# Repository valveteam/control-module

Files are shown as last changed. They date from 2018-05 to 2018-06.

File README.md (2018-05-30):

# control-module
Control module for the valve

This repository contains;
* The Arduino code for flow control module
* A test file & I2C Scan program for debugging
* CAD File for the control module using an Arduino Micro as the Microcontroller
* CAD File for the control module using an Arduino Nano as the Microcontroller (Outdated)
 
## Notes
* The final design was implemented with the Micro so the CAD files are slightly outdated (the NMOS buffer circuits and additional trimmer not included)

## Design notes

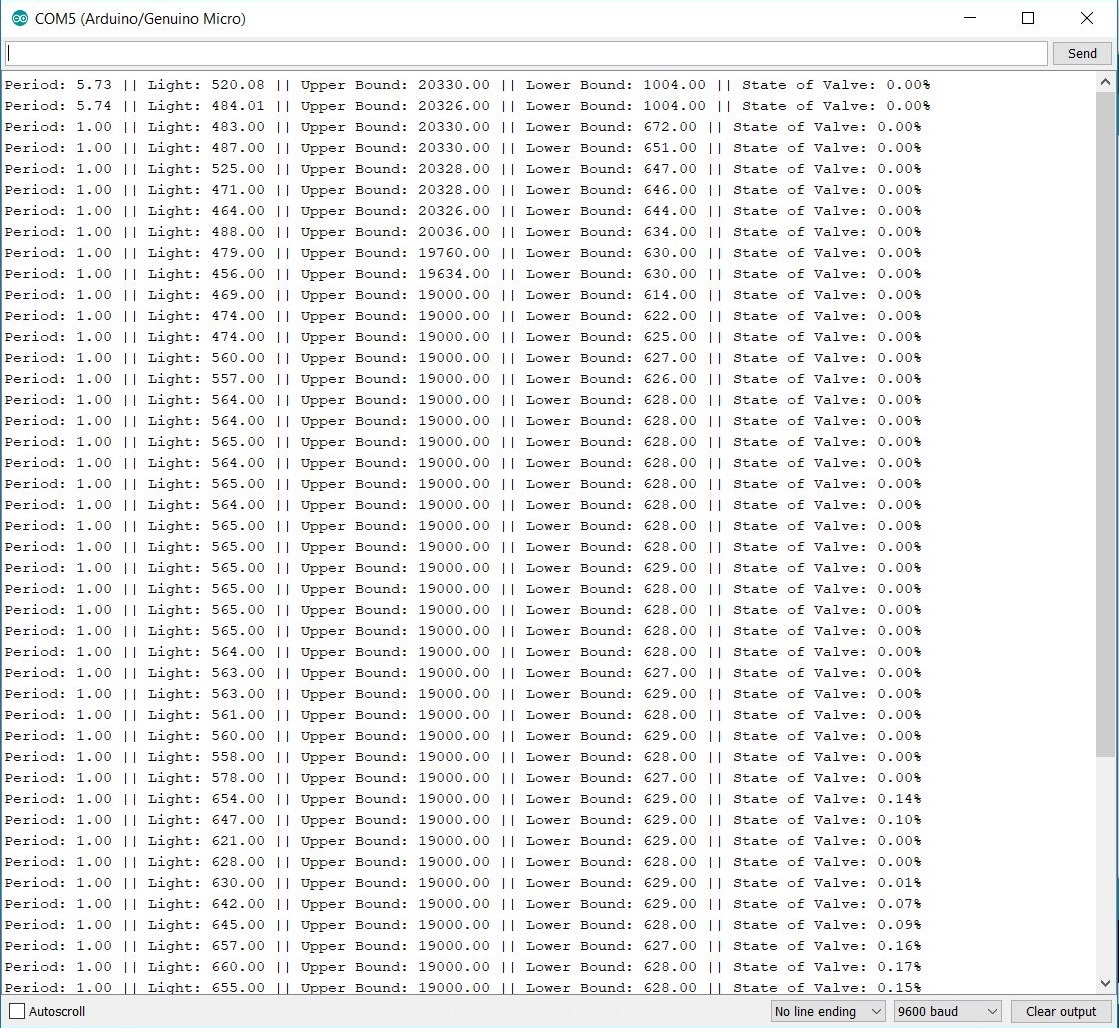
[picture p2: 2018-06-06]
Code/Control/control_bh1750/serial_output.JPG

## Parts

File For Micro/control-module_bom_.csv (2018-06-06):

Component | Description | Part | References | Value | Footprint | Quantity Per PCB | Datasheet
1 | Unpolarized capacitor | C | C1 C2 C3 C4 | 10uF | C_0805_HandSoldering | 4
2 |  | LED-RESCUE-control-module | D1 D2 D3 D4 | LED | LED_0805_HandSoldering | 4
3 |  | I2C-PCA9517 | I2Crepeater1 I2Crepeater2 | I2C-PCA9517 | TSSOP-8_3x3mm_Pitch0.65mm | 2
4 | Generic connector, single row, 01x06 | Conn_01x06 | J1 | For Expansion | Molex_KK-6410-06_06x2.54mm_Straight | 1
5 | Generic connector, single row, 01x06 | Conn_01x06 | J6 | For Flow Module a | Molex_KK-6410-06_06x2.54mm_Straight | 1
6 | Generic connector, single row, 01x06 | Conn_01x06 | J5 | For Flow Module b | Molex_KK-6410-06_06x2.54mm_Straight | 1
7 | Generic connector, single row, 01x06 | Conn_01x06 | J2 | For Light Sensor | Molex_KK-6410-06_06x2.54mm_Straight | 1
8 | Generic connector, single row, 01x02 | Conn_01x02 | J3 | From Solar Panel | TE_TERM | 1
9 | Generic connector, single row, 01x02 | Conn_01x02 | J4 | To Flow Module (F) | TE_TERM | 1
10 | Jumper, normally open | Jumper_NO_Small | JP1 JP2 JP3 | Jumper_NO_Small | SMD-solder-bridge | 3
11 |  | INDUCTOR | L1 L2 | 6.8uH | WURTH_INDUCTOR | 2
12 | Transistor N-MOSFET (general) | Q_NMOS_DGS | Q1 Q2 Q3 Q4 | NMOS | SOT-23_Handsoldering | 4
13 | Resistor | R | R1 R2 | 4.7k | R_0805_HandSoldering | 2
14 | Resistor | R | R4 R5 R6 | 470 | R_0805_HandSoldering | 3
15 | Resistor | R | R3 | 680 | R_0805_HandSoldering | 1
16 | Trim-Potentiometer | POT_TRIM | RV2 | Trimmer Lower | Potentiometer_Trimmer_Vishay_T73XX_Vertical | 1
17 | Trim-Potentiometer | POT_TRIM | RV1 RV3 | Trimmer Upper | Potentiometer_Trimmer_Vishay_T73XX_Vertical | 2
18 | Arduino Micro shield | ARDUINO_MICRO_SHIELD | U3 | ARDUINO_MICRO_SHIELD | ARDUINO_MICRO_SHIELD | 1
19 | Linear Regulator +5V | TR_SERIES | U1 U2 | TR_SERIES | TR_Series | 2 | regulator\lm78xx.pdf
Component Groups: | 19
Component Count: | 37
Fitted Components: | 37
Number of PCBs: | 1
Total components: | 37
Schematic Version:
Schematic Date:
BoM Date: | 04/06/2018 09:44:44
Schematic Source: | C:/Users/tooyi/Dropbox/tfpb/control-module/For Micro/control-module.sch
KiCad Version: | Eeschema 4.0.7

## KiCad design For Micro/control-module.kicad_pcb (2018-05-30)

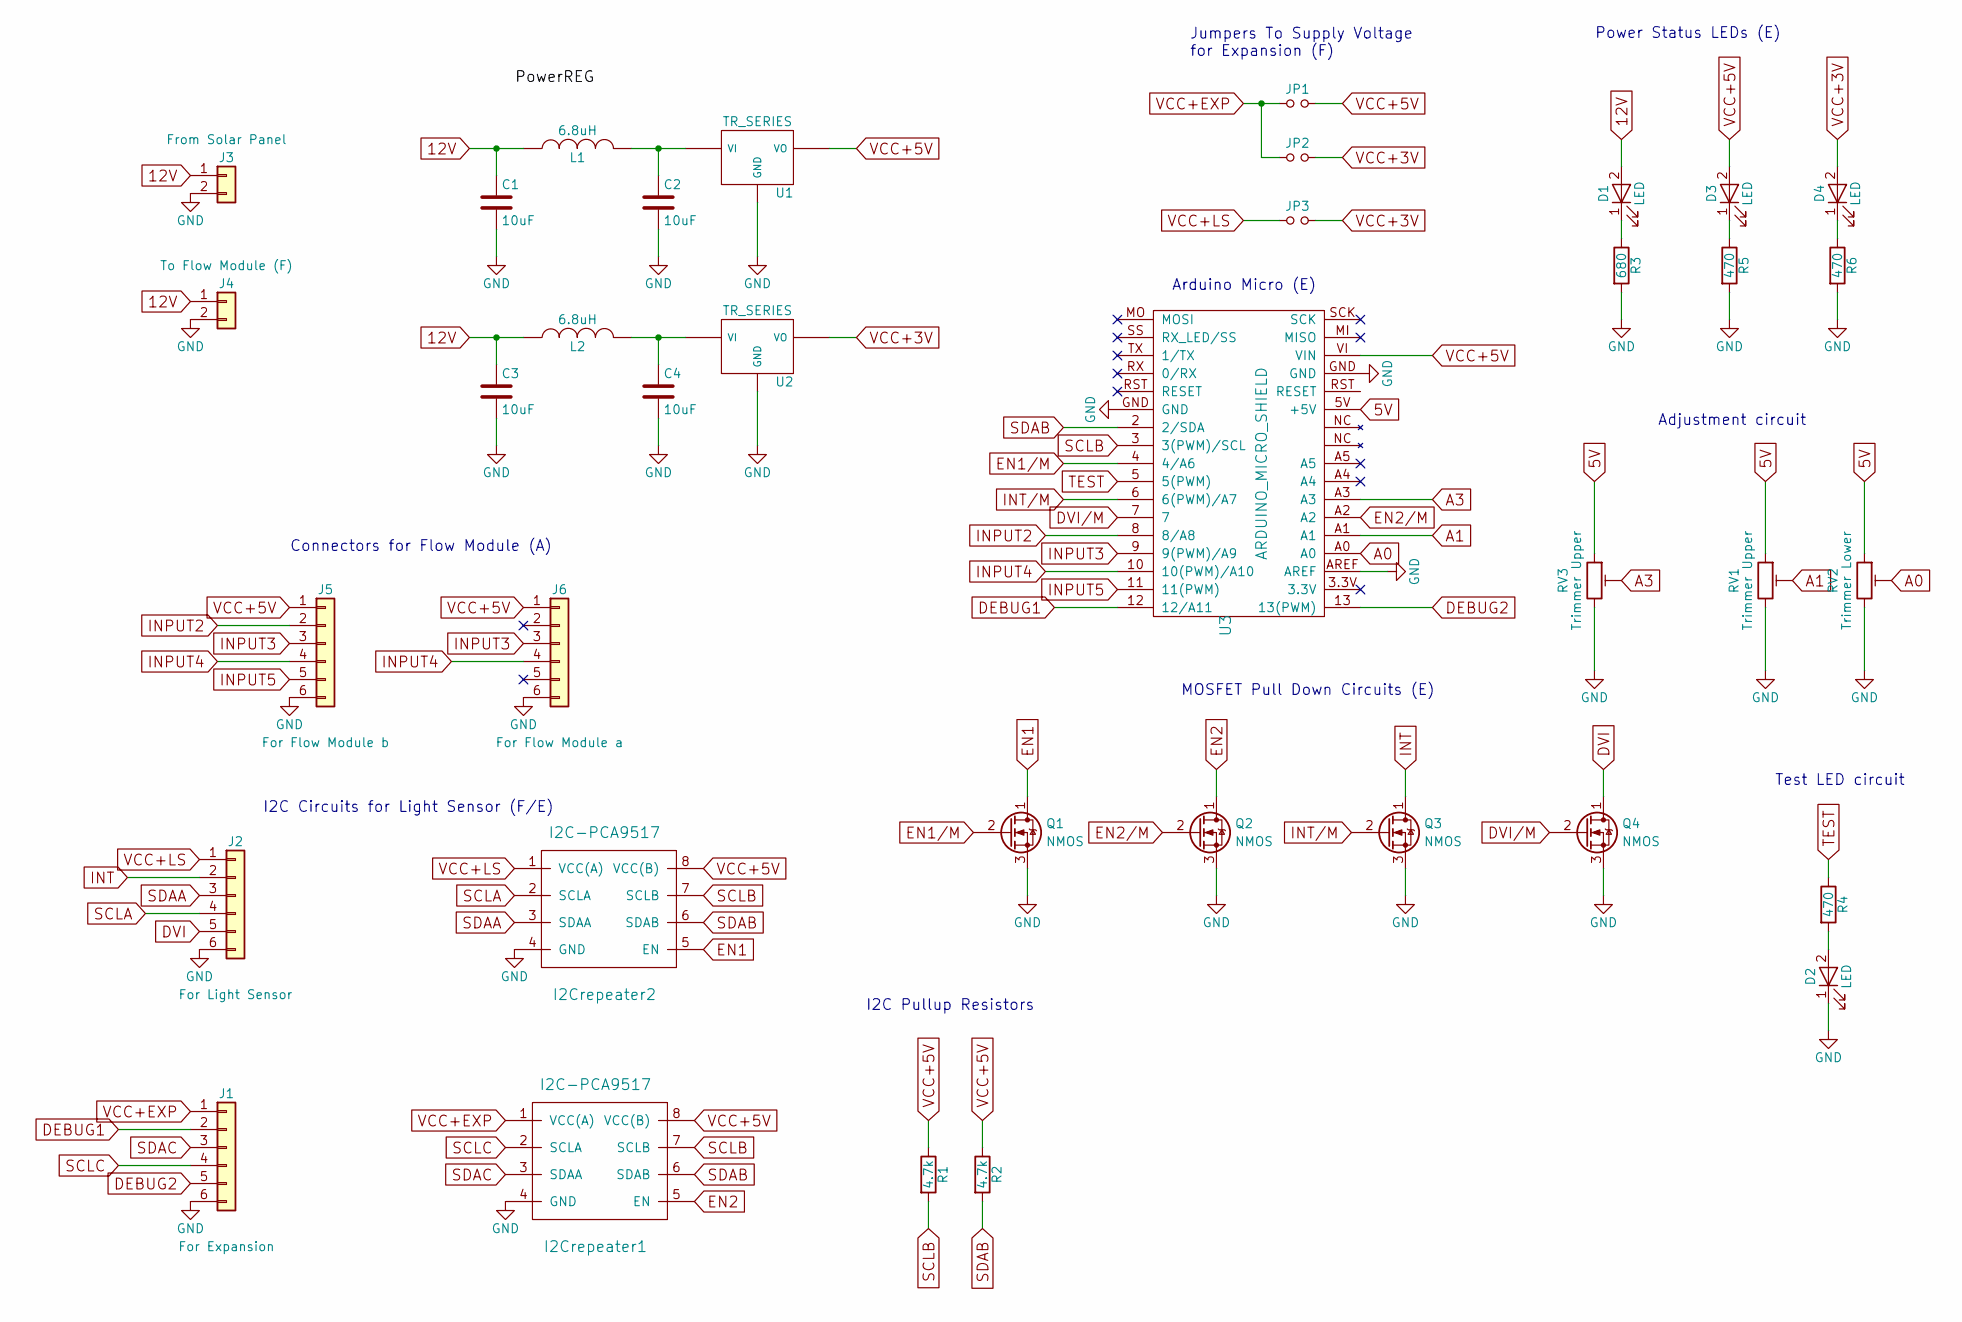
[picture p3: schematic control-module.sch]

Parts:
C1, C2, C3, C4: 10uF; C_0805_HandSoldering
D1, D2, D3, D4: LED; LED_0805_HandSoldering
I2Crepeater1, I2Crepeater2: I2C-PCA9517; TSSOP-8_3x3mm_Pitch0.65mm
J1: For Expansion; Molex_KK-6410-06_06x2.54mm_Straight
J2: For Light Sensor; Molex_KK-6410-06_06x2.54mm_Straight
J3: From Solar Panel; TE_TERM
J4: To Flow Module (F); TE_TERM
J5: For Flow Module b; Molex_KK-6410-06_06x2.54mm_Straight
J6: For Flow Module a; Molex_KK-6410-06_06x2.54mm_Straight
JP1, JP2, JP3: Jumper_NO_Small; SMD-solder-bridge
L1, L2: 6.8uH; WURTH_INDUCTOR
Q1, Q2, Q3, Q4: NMOS; SOT-23_Handsoldering
R1, R2: 4.7k; R_0805_HandSoldering
R3: 680; R_0805_HandSoldering
R4, R5, R6: 470; R_0805_HandSoldering
RV1, RV3: Trimmer Upper; Potentiometer_Trimmer_Vishay_T73XX_Vertical
RV2: Trimmer Lower; Potentiometer_Trimmer_Vishay_T73XX_Vertical
U1, U2: TR_SERIES; TR_Series
U3: ARDUINO_MICRO_SHIELD

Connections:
5V: RV1.1, RV2.1, RV3.1, U3.5V (+5V)
12V: C1.1, C3.1, D1.2 (A), J3.1, J4.1, L1.1, L2.1
A0: RV2.2, U3.A0
A1: RV1.2, U3.A1
A3: RV3.2, U3.A3
DEBUG1: J1.2, U3.12 (12/A11)
DEBUG2: J1.5, U3.13 (13(PWM))
DVI: J2.5, Q4.1 (D)
DVI/M: Q4.2 (G), U3.7
EN1: I2Crepeater2.5 (EN), Q1.1 (D)
EN1/M: Q1.2 (G), U3.4 (4/A6)
EN2: I2Crepeater1.5 (EN), Q2.1 (D)
EN2/M: Q2.2 (G), U3.A2
GND: C1.2, C2.2, C3.2, C4.2, D2.1 (K), I2Crepeater1.4 (GND), I2Crepeater2.4 (GND), J1.6, J2.6, J3.2, J4.2, J5.6, J6.6, Q1.3 (S), Q2.3 (S), Q3.3 (S), Q4.3 (S), R3.2, R5.2, R6.2, RV1.3, RV2.3, RV3.3, U1.GND, U2.GND, U3.AREF, U3.GND
INPUT2: J5.2, U3.8 (8/A8)
INPUT3: J5.3, J6.3, U3.9 (9(PWM)/A9)
INPUT4: J5.4, J6.4, U3.10 (10(PWM)/A10)
INPUT5: J5.5, U3.11 (11(PWM))
INT: J2.2, Q3.1 (D)
INT/M: Q3.2 (G), U3.6 (6(PWM)/A7)
unnamed: C2.1, L1.2, U1.VI
unnamed: C4.1, L2.2, U2.VI
unnamed: D1.1 (K), R3.1
unnamed: D2.2 (A), R4.2
unnamed: D3.1 (K), R5.1
unnamed: D4.1 (K), R6.1
SCLA: I2Crepeater2.2 (SCLA), J2.4
SCLB: I2Crepeater1.7 (SCLB), I2Crepeater2.7 (SCLB), R1.2, U3.3 (3(PWM)/SCL)
SCLC: I2Crepeater1.2 (SCLA), J1.4
SDAA: I2Crepeater2.3 (SDAA), J2.3
SDAB: I2Crepeater1.6 (SDAB), I2Crepeater2.6 (SDAB), R2.2, U3.2 (2/SDA)
SDAC: I2Crepeater1.3 (SDAA), J1.3
TEST: R4.1, U3.5 (5(PWM))
VCC+3V: D4.2 (A), JP2.2, JP3.2, U2.VO
VCC+5V: D3.2 (A), I2Crepeater1.8 (VCC(B)), I2Crepeater2.8 (VCC(B)), J5.1, J6.1, JP1.2, R1.1, R2.1, U1.VO, U3.VI (VIN)
VCC+EXP: I2Crepeater1.1 (VCC(A)), J1.1, JP1.1, JP2.1
VCC+LS: I2Crepeater2.1 (VCC(A)), J2.1, JP3.1

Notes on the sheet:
Adjustment circuit
Test LED circuit
I2C Circuits for Light Sensor (F/E)
Connectors for Flow Module (A)
Power Status LEDs (E)
MOSFET Pull Down Circuits (E)
I2C Pullup Resistors
Arduino Micro (E)
Jumpers To Supply Voltage for Expansion (F)

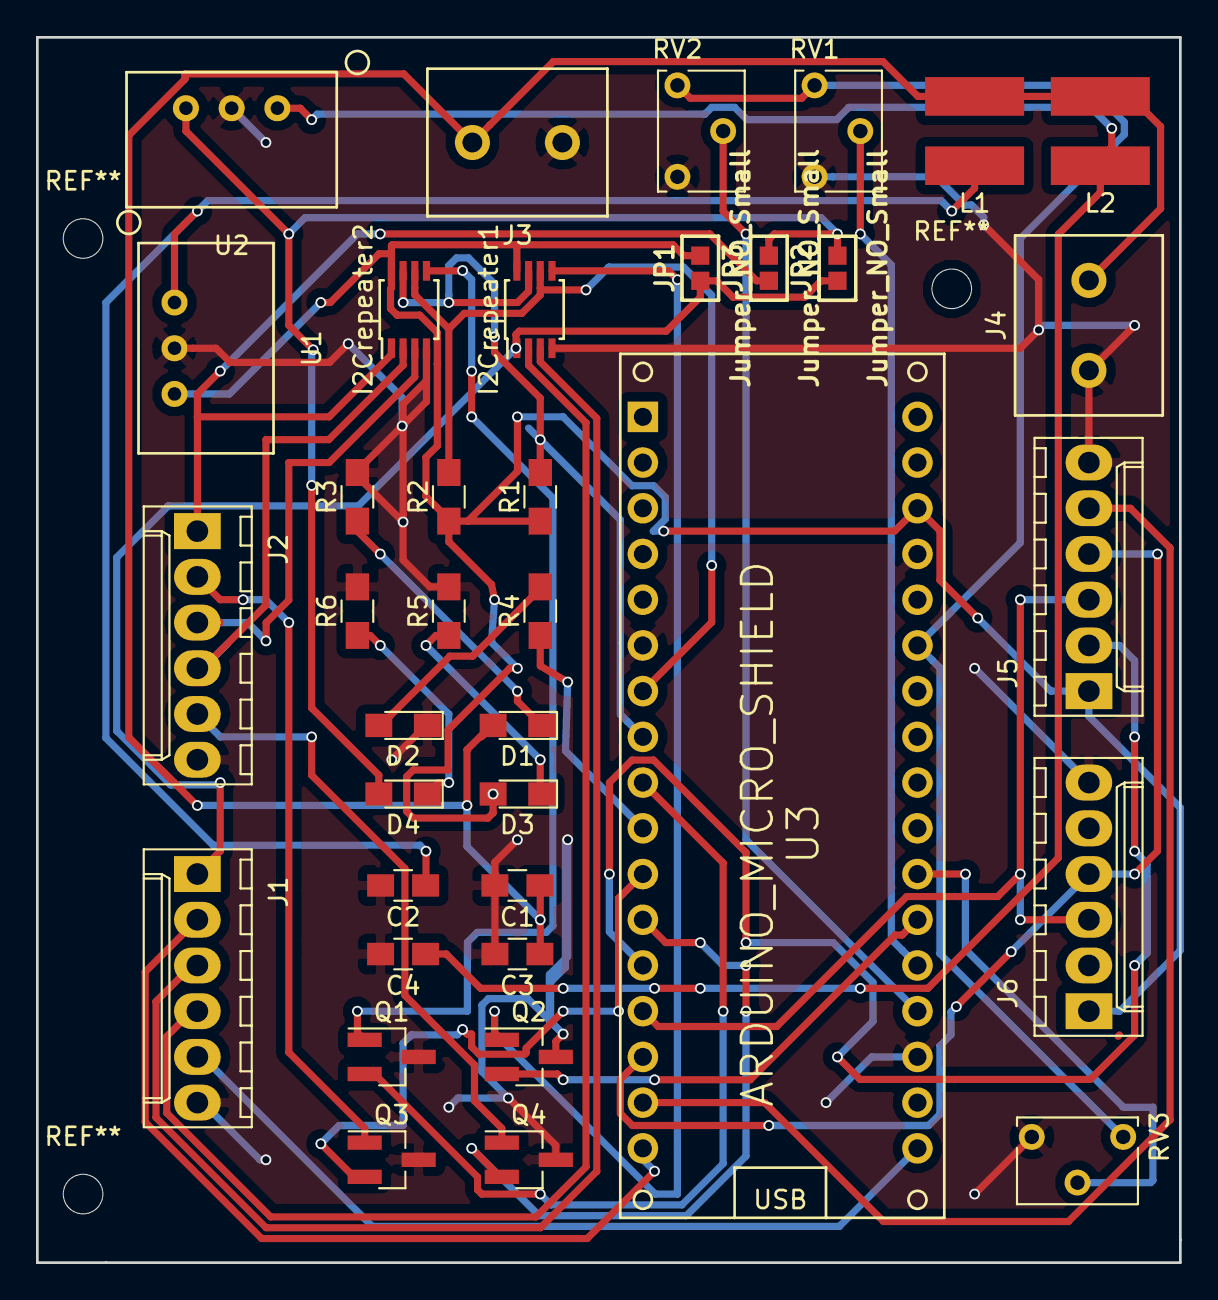
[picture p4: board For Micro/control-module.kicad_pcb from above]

Board: 2 copper layers, 63.5 x 68.1 mm, 37 parts (0 on the bottom side), 37 nets.

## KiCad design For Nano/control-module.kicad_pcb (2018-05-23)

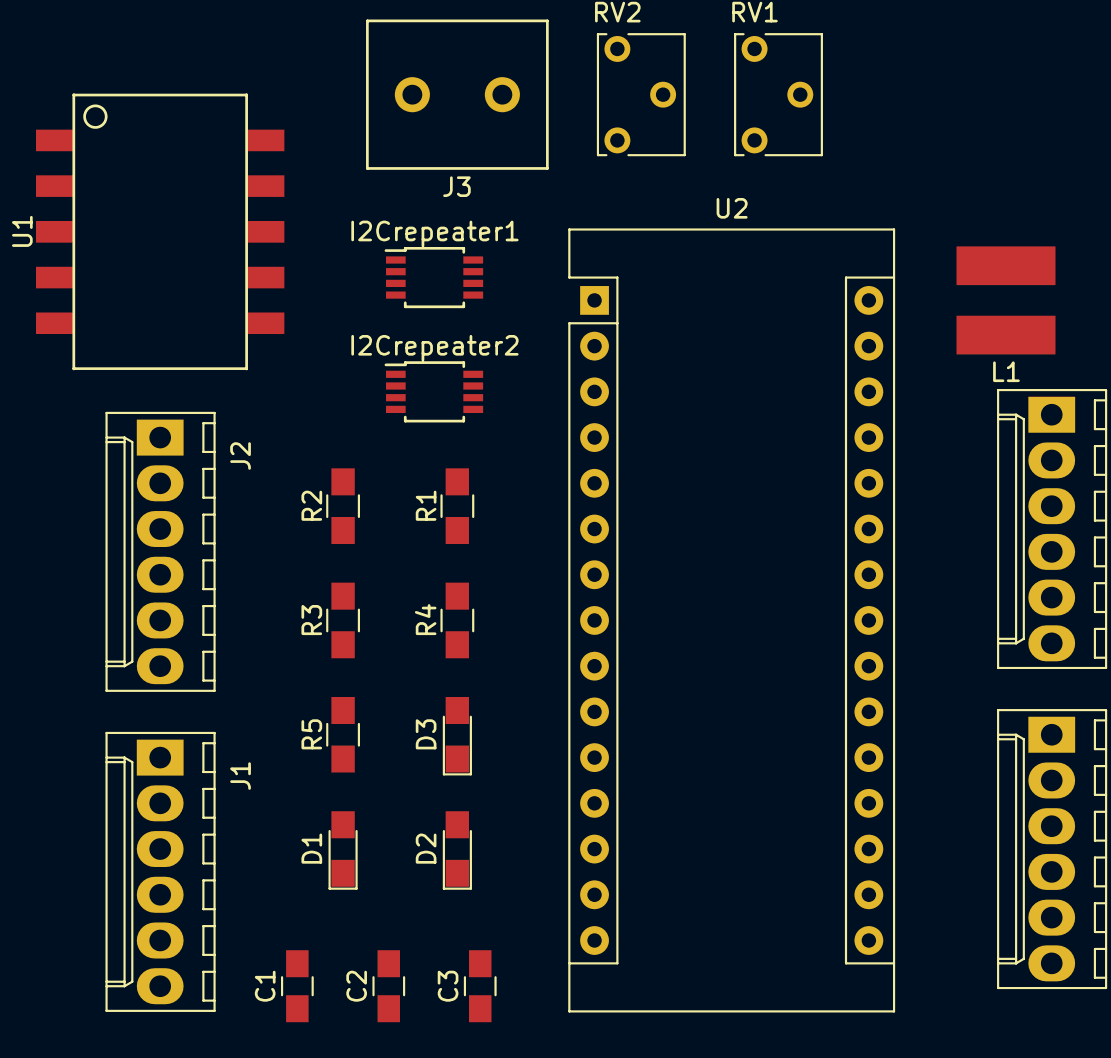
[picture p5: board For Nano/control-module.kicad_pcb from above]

Board: 2 copper layers, 23 parts (0 on the bottom side), 22 nets, no tracks yet.

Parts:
C1, C2, C3: 4.7uF; C_0805_HandSoldering
D1, D2, D3: LED; LED_0805_HandSoldering
I2Crepeater1, I2Crepeater2: I2C-PCA9517; TSSOP-8_3x3mm_Pitch0.65mm
J1, J2: For Light Sensor; Molex_KK-6410-06_06x2.54mm_Straight
J3: From Solar Panel; TE_TERM
J4: For Flow Module b; Molex_KK-6410-06_06x2.54mm_Straight
J5: For Flow Module a; Molex_KK-6410-06_06x2.54mm_Straight
L1: 3.3uH; WURTH_INDUCTOR
R1, R2: 4.7k; R_0805_HandSoldering
R3: 680; R_0805_HandSoldering
R4, R5: 150; R_0805_HandSoldering
RV1: Trimmer Upper; Potentiometer_Trimmer_Vishay_T73XX_Vertical
RV2: Trimmer Lower; Potentiometer_Trimmer_Vishay_T73XX_Vertical
U1: STR05
U2: Arduino_Nano_R3; Arduino_Nano

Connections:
5V: RV1.1, RV2.1, U2.12
12V: C1.1, C2.1, J3.1, L1.1, R3.1
A0: RV2.2, U2.4
A1: RV1.2, U2.5
DEBUG1: J1.2, U2.17
DEBUG2: J1.5, U2.16
DVI: J2.5, U2.21
GND: C1.2, C2.2, C3.2, D1.1, D2.1, D3.1, J1.6, J2.6, J3.2, J4.6, J5.6, RV1.3, RV2.3, U1.GND, U2.3, U2.14, U2.19
INPUT2: J4.2, U2.26
INPUT3: J4.3, J5.3, U2.27
INPUT4: J4.4, J5.4, U2.28
INPUT5: J4.5, U2.29
INT: J2.2, U2.20
unnamed: D1.2, R3.2
unnamed: D2.2, R4.2
unnamed: D3.2, R5.2
unnamed: L1.2, U1.VI
SCLB: R1.2, U2.23
SDAB: R2.2, U2.22
TEST: R4.1, U2.1
VCC+3V: J1.1, J2.1
VCC+5V: J4.1, J5.1, R1.1, R2.1, R5.1, U1.VO, U2.15

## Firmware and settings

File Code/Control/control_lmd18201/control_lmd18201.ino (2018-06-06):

// NOTE: This file pinouts is currently set up to control the LMD18201 H=Bridge - needs to be adapted for the other one!!!!!

#include <Wire.h>
#include <BH1750.h>

// address from datasheet
BH1750 lightMeter(0x5c);

//INITIALISATION
//Pin Assignments
int dviPin = 4;
int en1Pin = 5;
int en2Pin = A2;
int intPin = 6;
//direction
int sPin1 = 8;
// brake
int sPin2 = 9;
// this is the PWM output for the LMD18201
int sPin3 = 10;
// this is the thermal flag input for the LMD18201
int sPin4 = 11;
int debugPin1 = 12;
int debugPin2 = 13;
int analogPin1 = A0;
int analogPin2 = A1;
int analogPin3 = A3;

//Variables
float lBound = 0;
float uBound = 0;
float pWidth = 0;
float tau=0;
uint16_t lux = 0;
float luxAvg = 0;
int i = 0;
float percentage =0;

//SETUP
void setup() 
{
  Serial.begin(9600);

  // put your setup code here, to run once:
  pinMode(dviPin, OUTPUT);
  pinMode(en1Pin, OUTPUT);
  pinMode(en2Pin, OUTPUT);
  pinMode(intPin, OUTPUT);
  pinMode(sPin1, OUTPUT);
  pinMode(sPin2, OUTPUT);
  pinMode(sPin3, OUTPUT);
  pinMode(sPin4, INPUT);
  pinMode(debugPin1, OUTPUT);
  pinMode(debugPin2, OUTPUT);
  pinMode(LED_BUILTIN, OUTPUT);

  // Initialize the I2C bus (BH1750 library doesn't do this automatically)
  // On esp8266 devices you can select SCL and SDA pins using Wire.begin(D4, D3);
  Wire.begin();
  lightMeter.begin();
  Serial.println(F("BH1750 Test"));

  //Setup of valve is OFF
  // set brake and direction low. 
  digitalWrite(sPin1, LOW);
  digitalWrite(sPin2, LOW);

  // default: valve closed
  digitalWrite(sPin3, LOW);
}

//LOOP
void loop() 
{ 
  //Changing pulse width
  // note that analog read is between 0 and 1023
  pWidth = 1000 + (9000.00*analogRead(analogPin3)/1023.00); //goes from 1 Hz to 0.1 Hz.
  
  //tuning circuit
  Serial.println(analogRead(analogPin1));
  Serial.println(analogRead(analogPin2));
  lBound = analogRead(analogPin1) + 500; // lower bound from 500 - 1523
  uBound = (analogRead(analogPin2)*2) + 19000; //upper bound from 19000 - 21046 

  //BH1750 - reading light levels
  //Averages the light level wrt pWidth
  luxAvg=0;
  while (i<pWidth)
  {
    lux = lightMeter.readLightLevel();
    luxAvg = luxAvg+lux;
    i++;
  };
  luxAvg = luxAvg/pWidth;

  i=0;
  
  //Reading knobs & calculating tau wrt to lux levels
  if(lux > uBound) //avoids case tau larger pWidth
  {
    //solenoid fully open
    tau = pWidth;
    digitalWrite(sPin3, HIGH);
    digitalWrite(LED_BUILTIN, HIGH);
    delay(pWidth);
  } else if(lux < lBound) //avoids cause tau less than pWidth
  {
    //solenoid fully closed
    tau = 0;
    digitalWrite(sPin3, LOW);
    digitalWrite(LED_BUILTIN, LOW);
    delay(pWidth);
  } else 
  {
    //solenoid varying
    tau = pWidth*((lux-lBound)/(uBound-lBound)); //goes to zero when lux is at lBound and to one when lux is at uBound
    digitalWrite(sPin3, HIGH);
    digitalWrite(LED_BUILTIN, HIGH); 
    delay(tau);                       
    digitalWrite(sPin3, LOW);
    digitalWrite(LED_BUILTIN, LOW);
    delay(pWidth-tau);
  };

  percentage = (tau*100)/pWidth;  
  //Reading Serial Port for Debug
  Serial.print("Period: ");  
  Serial.print(pWidth/1000);
  Serial.print(" || "); 
  Serial.print("Light: ");  
  Serial.print(luxAvg); 
   Serial.print(" || ");
   Serial.print("Upper Bound: ");  
  Serial.print(uBound);
  Serial.print(" || "); 
  Serial.print("Lower Bound: ");  
  Serial.print(lBound);
  Serial.print(" || ");  
  Serial.print("State of Valve: ");  
  Serial.print(percentage); 
  Serial.println("%"); 
  
}

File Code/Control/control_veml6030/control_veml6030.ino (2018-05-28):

#include <Wire.h>
#include <VEML6030.h>

VEML6030 ALS;

//INITIALISATION
//Pin Assignments
int dviPin = 4;
int enPin = 5;
int intPin = 6;
int sPin1 = 8;
int sPin2 = 9;
int sPin3 = 10;
int sPin4 = 11;
int debugPin1 = 12;
int debugPin2 = 13;
int analogPin1 = A0;
int analogPin2 = A1;
//Variables
float lbound = 0;
float ubound = 0;
float tau = 0;
uint8_t lux = 0;

//SETUP
void setup() 
{
  Serial.begin(9600);

  // put your setup code here, to run once:
  pinMode(dviPin, OUTPUT);
  pinMode(enPin, OUTPUT);
  pinMode(intPin, OUTPUT);
  pinMode(sPin1, OUTPUT);
  pinMode(sPin2, OUTPUT);
  pinMode(sPin3, OUTPUT);
  pinMode(sPin4, OUTPUT);
  pinMode(debugPin1, OUTPUT);
  pinMode(debugPin2, OUTPUT);
  pinMode(LED_BUILTIN, OUTPUT);

  // On esp8266 devices you can select SCL and SDA pins using Wire.begin(D4, D3);
  Wire.begin();
  ALS.begin(0x10);; //Begin the UV module
  Serial.println(F("VEML6030 Test"));

  //Setup of valve is OFF
  digitalWrite(sPin1, LOW);
  digitalWrite(sPin2, LOW);
  digitalWrite(sPin3, LOW);
  digitalWrite(sPin4, LOW);
}

//LOOP
void loop() 
{
  //tuning circuit
  lbound = analogRead(analogPin1) + 500; // lower bound from 500 - 1500
  ubound = (analogRead(analogPin2)*2) + 19000; //upper bound from 19000 - 21000
  
  //VEML6030 - reading light levels
  ALS.AutoRange();
  lux = ALS.GetLux();
  Serial.print("Light: ");
  Serial.println(lux);
  
  //Control
  if(lux > ubound)
  {
    //solenoid at max
    tau = 1000;
    digitalWrite(sPin2, HIGH);
    digitalWrite(LED_BUILTIN, HIGH); 
    delay(tau);                       
    digitalWrite(sPin2, LOW);
    digitalWrite(LED_BUILTIN, LOW);
    delay(1000-tau);
  } else if(lux < lbound)
  {
    //turning solenoid off
    digitalWrite(sPin2, LOW);
    digitalWrite(sPin3, LOW);
    digitalWrite(LED_BUILTIN, LOW);
    delay(1000);
  } else
  {
    //solenoid varying
    tau = 1000*(lux/(ubound));
    digitalWrite(sPin2, HIGH);
    digitalWrite(LED_BUILTIN, HIGH); 
    delay(tau);                       
    digitalWrite(sPin2, LOW);
    digitalWrite(LED_BUILTIN, LOW);
    delay(1000-tau);
  };
  
}

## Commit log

2018-05-23 included I2c repeater
    [_saved_control-module.sch, control-module.kicad_pcb, control-module.sch]
2018-05-23 First draft
    [_saved_control-module.sch]
2018-05-23 PCB Layout for Control Module
    [control-module.kicad_pcb, control-module.sch]
2018-05-25 Updated code for Arduino Micro
    [control-module.kicad_pcb, control-module.sch]
2018-05-26 Code with most functionality - not tested
    Added a "PWM" that changes value of tau from 0 - 1000, which would determine the proportion of time the valve is open.
    Using wikipedia, assumed upper bound to be around 20000 lux and lower bound to be around 1000 lux.
    Removed some bugs.
    [control.ino]
2018-05-27 Folder management and wrote code for VEML6030
    Successfully Compiled but not verified.
    Also, VEML returns uint_8 vs uint_16, have to dig into driver files to edit if more precision needed.
2018-05-28 removed bugs, set led to blink depending on signal
    [control_bh1750.ino, control_veml6030.ino, solenoid_test.ino]
2018-05-28 Cleaned up control code, verified at this point. Added NMOS to Control CAD
    [control-module.kicad_pcb, control-module.sch]
2018-05-28 Test circuit for solenoid and light
2018-05-29 Add MOSFET circuits, power LED, regulator, connector and jumpers
    [control-module.sch]
2018-05-29 PCB for Control
    [control-module.kicad_pcb, control-module.sch]
2018-05-29 Update netlist and pcb with fixed I2C repeater
    [control-module.kicad_pcb]
2018-05-30 Final CAD for Micro
    [control-module.kicad_pcb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]
2018-06-04 Bill of Materials
    [control-module_bom_.csv]
